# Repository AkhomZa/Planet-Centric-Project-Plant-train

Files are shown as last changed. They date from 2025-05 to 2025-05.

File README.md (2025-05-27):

# Planet Centric Project : Plant train
โปรเจคนี้เป็นของวิชา FRA503 : PLANET-CENTRIC ROBOTICS &amp; INNOVATION

ผูัจัดทำ : อาคม สนธิขันธ์

# แนวคิดและที่มา
การปลูกต้นไม้บนโต๊ะทำงานไม่เพียงช่วยสร้างบรรยากาศที่ร่มรื่นและน่าอยู่เท่านั้น แต่ยังมีส่วนช่วยฟอกอากาศและส่งเสริมสุขภาพจิตของผู้ปฏิบัติงานอีกด้วย หลายงานวิจัยชี้ว่าการมีต้นไม้ในพื้นที่ทำงานสามารถลดความเครียด เพิ่มสมาธิ และสร้างความรู้สึกผ่อนคลาย ส่งผลให้เกิดประสิทธิภาพในการทำงานที่ดีขึ้น ดังนั้นแนวคิดการปลูกต้นไม้บนโต๊ะทำงานจึงเป็นจุดเริ่มต้นของโครงการนี้

ในปัจจุบันมีนวัตกรรมต้นไม้แบบอัจฉริยะ เช่น Smart Plant Ivy ซึ่งรวมเซนเซอร์วัดค่าความชื้น แสง และระบบควบคุมต่างๆ ไว้ในกระถางต้นไม้เดียว อย่างไรก็ตาม หากต้องการปลูกหลายต้น ก็จำเป็นต้องมีเซนเซอร์และอุปกรณ์แยกในแต่ละกระถาง ซึ่งทำให้ต้นทุนสูงขึ้นอย่างไม่จำเป็น

เพื่อแก้ปัญหาดังกล่าว ผู้จัดทำจึงเสนอแนวคิดการรวมระบบเซนเซอร์ไว้ในจุดเดียว และออกแบบให้แต่ละกระถางสามารถใช้เซนเซอร์ร่วมกันได้ เพื่อลดค่าใช้จ่ายและความซับซ้อนของระบบ

อีกหนึ่งปัญหาที่พบในการปลูกต้นไม้บนโต๊ะทำงานคือ “ตำแหน่งการวางกระถาง” หากวางไว้ในบริเวณที่แสงไม่เพียงพอ ต้นไม้อาจไม่เจริญเติบโตหรือตายได้

จากปัญหาและแนวคิดข้างต้น จึงได้ออกแบบนวัตกรรม "กระถางต้นไม้เคลื่อนที่ได้" ซึ่งสามารถเคลื่อนย้ายตัวเองเพื่อหาตำแหน่งที่มีแสงเหมาะสม และสามารถวัดค่าต่างๆ ผ่านเซนเซอร์ส่วนกลางร่วมกันได้ ช่วยเพิ่มโอกาสในการเจริญเติบโตของพืช และยังลดต้นทุนในการติดตั้งระบบเซนเซอร์อีกด้วย

## Plant train

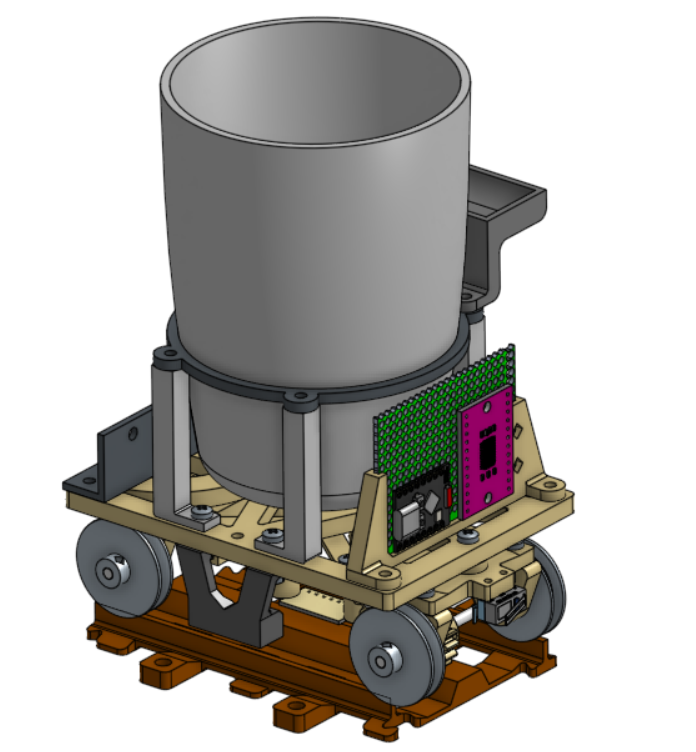
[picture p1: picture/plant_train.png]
Plant train


## Water station

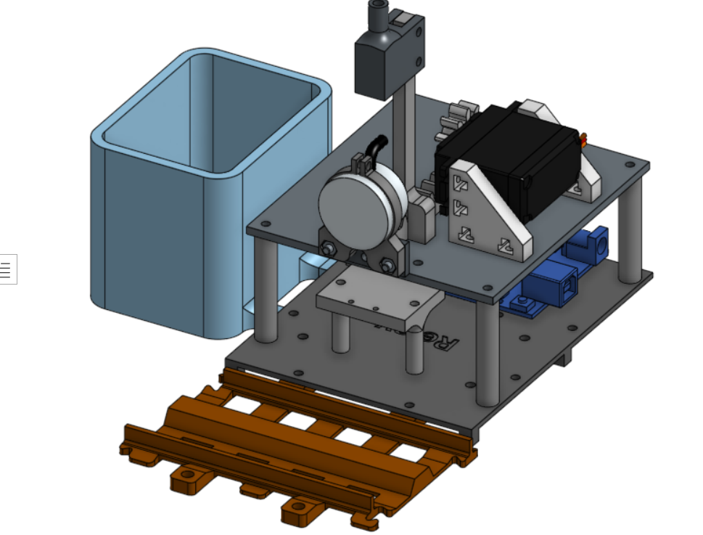
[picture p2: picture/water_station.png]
Water station


## Overview wiring diagram
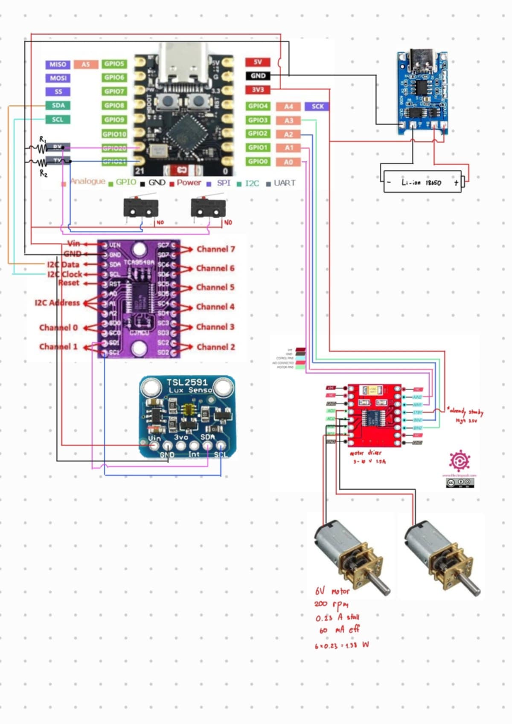
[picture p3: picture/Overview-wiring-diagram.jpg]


## Electronics Component

**"On Plant train"**

- **Microcontroller:** ESP32 C3 mini

- **Motor Driver:** DRV8833

- **Lux sensor:** BH1750 (วัดความเข้มของแสง)

- **Color sensor:** TCS34725 (สำหรับอ่านแถบสีคำสั่ง)

- **I2C Multiplexer:** TCA9548A (สำหรับขยายช่องสัญญาณ I2C)

- **Lithium Charging module:** USB TYPE-C charger TP4056 1A (สำหรับชาร์จแบตเตอรี่ลิเธียม 18650)

- **ฺBattery:** 186500 Lithium Battery

**"On Water station"**

- **Microcontroller:** Arduino Uno

- **Water level non contack sensor:** XKCY25 (วัดระดับน้ำแบบไร้สัมผัส)

- **Hall effect magnetic sensor:** KY-035 (สำหรับตรวจเช็คการมาของรถไฟ)

- **Relay module:** 4 channel-Relay

- **DC Water pump**

- **Servo motor:** MG995 180 degree servo motor

## Mechanics Part

- **3D Print part**

- **Shaft diameter:** 3 mm

- **Bearing:** 603ZZ

- **O-ring:** ID 19 mm 2 mm thickness

- **Heat brass insert**

- **Bolt&Nuts :** ส่วนใหญ่เป็นขนาด M3 ยาว 6-12 mm ขึ้นอยู่กับส่วนไหนใส่ได้ยาวแค่ไหน

## อุปกรณ์ที่เหลือ

- กระถางรดน้ำเอง แบบใช้หลักการกาลักน้ำ
- สายยางซิลิโคน ID 7 mm

## ภาพ CAD การประกอบคร่าวๆ และส่วนประกอบ

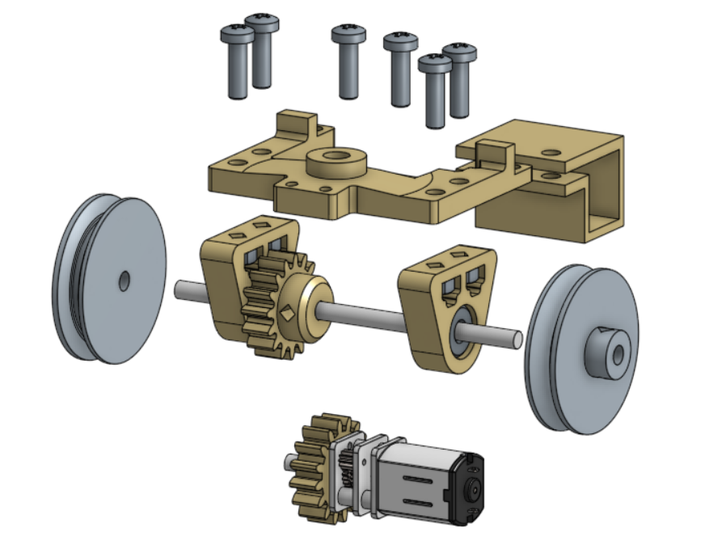
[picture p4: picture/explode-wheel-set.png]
Explode view of wheel set


- ใช้ shaft ประมาณ 65mm
- ใช้ set screw M3 กับล้อและเฟือง
- ประกอบส่วนล้อก่อนแล้วประกอบชุดมอเตอร์ทีหลัง
- ใส่เฟืองกับมอเตอร์ก่อนประกอบเข้าด้วยกัน
- ใช้ Screw M3*10 และ nut เป็นส่วนใหญ่

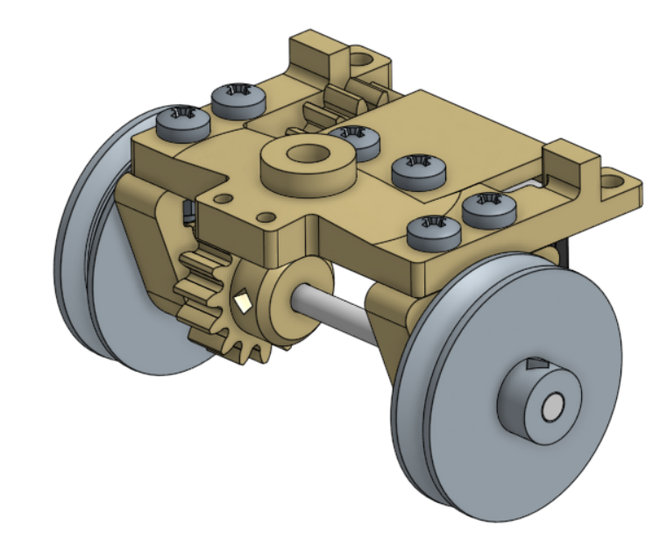
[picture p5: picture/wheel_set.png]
Wheel set assembly


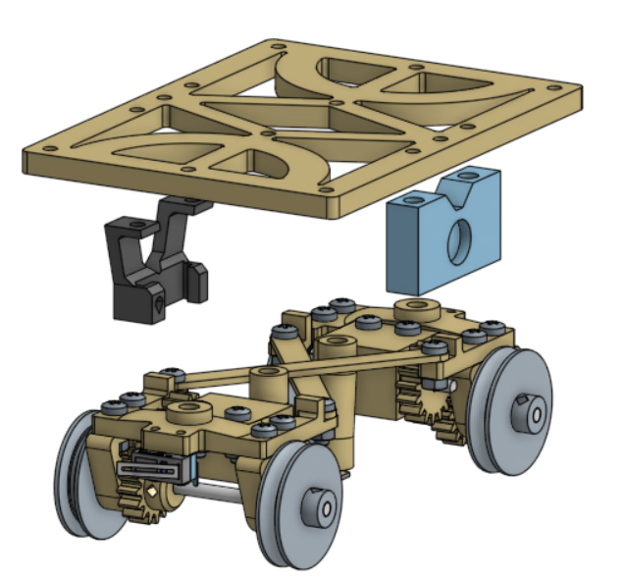
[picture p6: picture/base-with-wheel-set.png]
Base with wheel set assembly


- ประกอบ wheel set กับ base ด้วยสกรู M3*10 mm มันจะยึดไม่แน่นเพื่อให้รถสามารถเลี้ยวได้ สามารถเพิ่มเติมด้วยการใส่ น้ำยาล็อกเกลียวเพิ่ม เพื่อให้สกรูไม่คลาย หรือออกแบบใหม่ให้ดีขึ้น

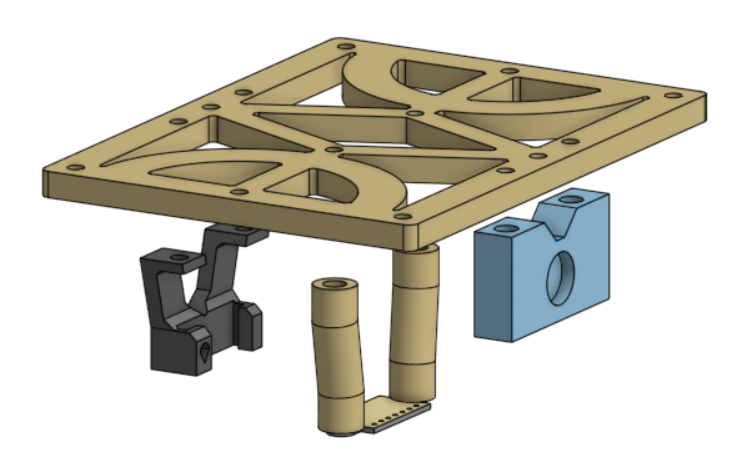
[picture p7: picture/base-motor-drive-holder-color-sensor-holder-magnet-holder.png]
Base with motor driver/magnet/color sensor holder


- spacer ยึด color sensor ทั้งสองด้านมี heat brass insert อยู่
- ประกับเซนเซอร์ก่อนค่อยประกอบกับ base
- ตัวยึด motor drive แนะนำให้ใส่ก่อนโดยการเลื่อนเข้าไปแล้วขันล็อกด้วย set screw M3 ก่อนแล้วบัดกรีสายไฟเข้าไป
- ตัวยึดแม่เหล็ก ก่อนใส่เช็คด้านของแม่เหล็กก่อน เพราะเอาออกยาก

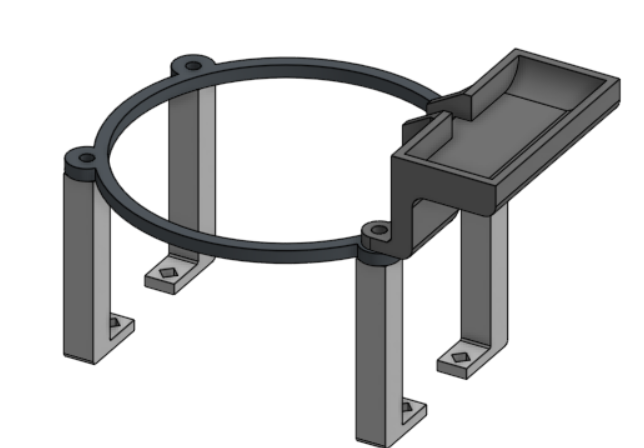
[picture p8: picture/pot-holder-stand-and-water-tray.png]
Pot holder with watering tray on top base


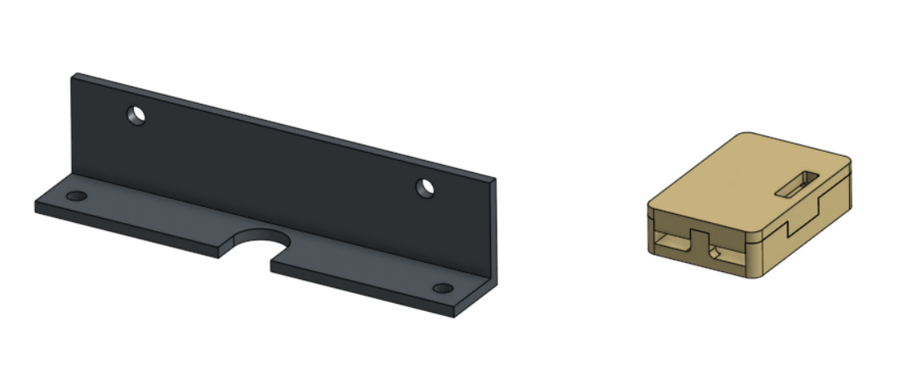
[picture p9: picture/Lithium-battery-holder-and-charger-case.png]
battery holder on the back and charger case


- ใช้กับรังถ่านแบตเตอรี่ลิเธียม 18650 แบบไม่มีสปริงขดลวด
- ใช้ Screw Tapor M3 แล้วล็อกด้วย nut
- บัดกรีสายไฟกับชุดชาร์จก่อนประกอบกับ case แล้วติดด้วยกาวสองหน้า

**ข้อสังเกตและการแนะนำ**
- รูขนาดประมาณ 4.5 mm สำหรับใส่ heat brass insert
- เริ่มประกอบจาก wheel set ก่อน ประกอบที่ล็อกมอเตอร์ และปิดป้ายด้วย X beam เชื่อม Wheel set 2 ชุดเข้าด้วยกัน

Water station

- ประกอบกับรางตรงเฉพาะแบบในรูปเท่านั้น
- ติดตั้ง relay และ arduino uno ก่อน ตามด้วยประกอบชั้นสองตาม
- ประกอบ servo โดยเซ็ตตำแหน่ง 0 องศาก่อน แล้วเลื่อน rack gear เข้าไป จุดท้ายประกอบ pinion gear ตามเข้าไป
  *จำเป็นออกแบบตัวติดตั้ง Hall effect magnetic sensor ใหม่

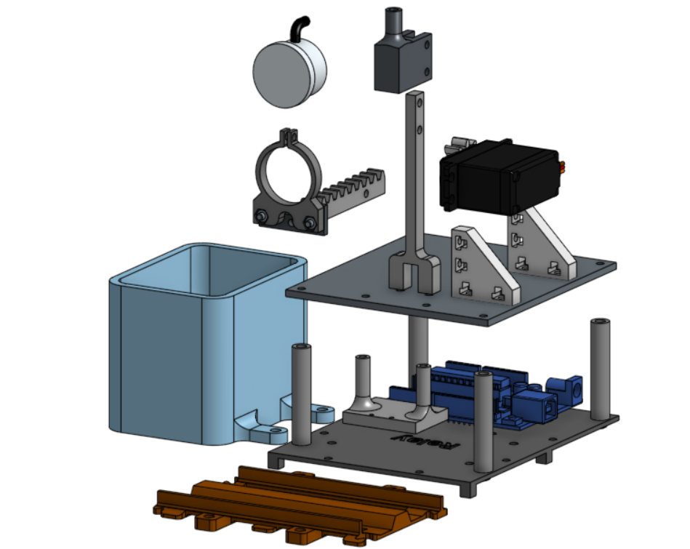
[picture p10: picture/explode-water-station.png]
Explode view Water station


## Code สำหรับตัวรถ

ก่อน upload เช็คหัวข้อ USB CDC On Boot หากใช้โปรแกรม Arduino IDE

```bash
#include <Wire.h>
#include <Adafruit_Sensor.h>
#include <Adafruit_TSL2591.h>
#include "TCA9548A.h"  //I2C multiplexer module
#include "Adafruit_TCS34725.h"
#include <BH1750.h>  //lux sensor module

#define commonAnode true
#define pwmA 0
#define in1A 1
#define in2A 2
#define pwmB 3
#define in1B 5
#define in2B 4
#define frontLimit 20
#define backLimit 21

TCA9548A mux;  //call multiplexer as mux

int LuxsensorState = 0;
unsigned long LuxlastReadTime = 0;
const unsigned long LuxsensorDelay = 5;

int ColorsensorState = 0;
unsigned long ColorlastReadTime = 0;
const unsigned long ColorsensorDelay = 5;

int countSun, countWater = 0;
bool trickDone = false;
float red, green, blue;
int WhiteTableOnRail_config[3] = {83,98,68};
int WhiteCode[3] = {70,101,75};
int RedCode[3] = {120,75,62};
int timeout = 30000;
float LeftFront, LeftBack, RightFront, RightBack; //for luxData

// Look from top view
//       front(B)
//      0 ------ 3
//          ||
//   left   ||   right
//          ||
//      1 ------ 2
//        back(A)
BH1750 lightMeter0(0x23);
BH1750 lightMeter1(0x23);
BH1750 lightMeter2(0x23);
BH1750 lightMeter3(0x23);

//color sensor config
Adafruit_TCS34725 tcs = Adafruit_TCS34725(TCS34725_INTEGRATIONTIME_50MS, TCS34725_GAIN_4X);

Adafruit_TSL2591 tsl = Adafruit_TSL2591(2591);

void lux_read(float* LeftFront, float* LeftBack, float* RightFront, float* RightBack);      // ประกาศฟังก์ชันที่อยู่ในไฟล์อื่น
void engine_start();  // ถ้าเรียกใช้ก็ประกาศไว้ด้วย

/* TCA9548A multi sent 0x29 for communicate TSL2591 so need to command to tca to tell tsl*/
void setup() {
  delay(1000);
  Serial.begin(115200);
  pinMode(pwmA, OUTPUT);
  pinMode(pwmB, OUTPUT);
  pinMode(in1A, OUTPUT);
  pinMode(in2A, OUTPUT);
  pinMode(in1B, OUTPUT);
  pinMode(in2B, OUTPUT);
  pinMode(frontLimit, INPUT);
  pinMode(backLimit, INPUT);
  Wire.begin(8, 9);  // GPIO 8 = SDA, GPIO 9 = SCL
  mux.begin(Wire);   // Use Wire instance
  mux.closeAll();    // Optional: reset all channels

  Serial.println(F("Starting"));

  //check lux sensor's read

  mux.openChannel(0);
  if (lightMeter0.begin(BH1750::CONTINUOUS_HIGH_RES_MODE)) {
    Serial.println(F("Left_Front sensor checked!"));
  } else {
    Serial.println(F("Left_Front sensor error!"));
  }
  delay(150);

  mux.openChannel(1);
  if (lightMeter1.begin(BH1750::CONTINUOUS_HIGH_RES_MODE)) {
    Serial.println(F("Left_Back sensor checked!"));
  } else {
    Serial.println(F("Left_Back sensor error!"));
  }
  delay(150);

  mux.openChannel(2);
  if (lightMeter2.begin(BH1750::CONTINUOUS_HIGH_RES_MODE)) {
    Serial.println(F("Right_Back sensor checked!"));
  } else {
    Serial.println(F("Right_Back sensor error!"));
  }
  delay(150);

  mux.openChannel(3);
  if (lightMeter3.begin(BH1750::CONTINUOUS_HIGH_RES_MODE)) {
    Serial.println(F("Right_Front sensor checked!"));
  } else {
    Serial.println(F("Right_Front sensor error!"));
  }
  delay(150);

  //check color sensor's status
  mux.openChannel(7);
  if (tcs.begin()) {
    Serial.println(F("TCS34725 COLOUR checked!"));
  } else {
    Serial.println(F("TCS34725 COLOUR not found!"));
  }
  delay(150);
  goWaterStation();
}

void loop() {
  int start_time = millis();
  while(millis() - start_time < 10000){
    followLight();
  }
  goWaterStation();
  delay(2000);

  // color_read();
}

/*funtion check water*/
void water_level() {
  /*506 mai jer
4095 jer*/
  if (analogRead(A0) >= 2300) {
    Serial.println("Water detected");
  } else {
    Serial.println("No Water");
  }
  delay(1000);
  // Serial.println(analogRead(A0));
}

/*function colour code*/
void track() {
  while (1) {
    if (digitalRead(frontLimit) == 1 && digitalRead(backLimit) == 1) {
      goFront(255, 255);
    } else if (digitalRead(frontLimit) == 0 && digitalRead(backLimit) == 1) {
      goBack(255, 255);
    } else if (digitalRead(frontLimit) == 0 && digitalRead(backLimit) == 0) {
      break;
    }
  }
}

void checkLimit() {  //limit switch active low
  if (digitalRead(frontLimit) == 0 && digitalRead(backLimit) == 1) {
    Serial.println("Front Limit Trigger");
  } else if (digitalRead(frontLimit) == 1 && digitalRead(backLimit) == 0) {
    Serial.println("Back Limit Trigger");
  } else if (digitalRead(frontLimit) == 0 && digitalRead(backLimit) == 0) {
    Serial.println("Both Limit Trigger");
  }
}

/* new code after test on I2C*/
void configureSensor(void) {
  tsl.setGain(TSL2591_GAIN_MED);
  tsl.setTiming(TSL2591_INTEGRATIONTIME_300MS);

  Serial.println(F("Sensor configured."));
}

void goFront(int MotorSpeed1, int MotorSpeed2) {
  int MotorStartSpeed1 = round((MotorSpeed1) / 3);
  int MotorStartSpeed2 = round((MotorSpeed2) / 3);
  digitalWrite(in1A, LOW);
  digitalWrite(in2A, HIGH);
  analogWrite(pwmA, MotorStartSpeed1);
  delay(50);
  digitalWrite(in1B, LOW);
  digitalWrite(in2B, HIGH);
  analogWrite(pwmB, MotorStartSpeed2);
  delay(100);
  analogWrite(pwmA, MotorSpeed1);
  delay(10);
  analogWrite(pwmB, MotorSpeed2);
}

void goBack(int MotorSpeed1, int MotorSpeed2) {
  int MotorStartSpeed1 = round((MotorSpeed1) / 3);
  int MotorStartSpeed2 = round((MotorSpeed2) / 3);
  digitalWrite(in1A, HIGH);
  digitalWrite(in2A, LOW);
  analogWrite(pwmA, MotorStartSpeed1);
  delay(50);
  digitalWrite(in1B, HIGH);
  digitalWrite(in2B, LOW);
  analogWrite(pwmB, MotorStartSpeed2);
  delay(100);
  analogWrite(pwmA, MotorSpeed1);
  delay(10);
  analogWrite(pwmB, MotorSpeed2);
}

void stop() {  // a is time in millisecond
  digitalWrite(in1A, LOW);
  digitalWrite(in2A, LOW);
  digitalWrite(in1B, LOW);
  digitalWrite(in2B, LOW);
}

void engine_start() {

  bool flag = false;
  Serial.println(digitalRead(frontLimit));
  Serial.println(digitalRead(backLimit));

  while (1) {
    if (digitalRead(frontLimit) == 0 && digitalRead(backLimit) == 0) {  //active low
      Serial.println("Ready");
      flag = true;
      break;
    } else
      Serial.println("Please hold 2 button to start!");
    delay(100);
  }
}

void color_read() {
  static int color_read[3];
  static int color_treshold = 5;

  mux.writeRegister(TCA_CHANNEL_7);
  delay(10);
  tcs.getRGB(&red, &green, &blue);
  color_read[0] = red;
  color_read[1] = green;
  color_read[2] = blue;
  delay(5);
  Serial.print("R:\t");
  Serial.print(int(red));
  Serial.print("\tG:\t");
  Serial.print(int(green));
  Serial.print("\tB:\t");
  Serial.print(int(blue));
  Serial.print("\n");
  if (abs(color_read[0] - WhiteCode[0]) < color_treshold && abs(color_read[1] - WhiteCode[1]) < color_treshold && abs(color_read[2] - WhiteCode[2]) < color_treshold) {
    Serial.print("White");
  }
  if (abs(color_read[0] - RedCode[0]) < color_treshold && abs(color_read[1] - RedCode[1]) < color_treshold && abs(color_read[2] - RedCode[2]) < color_treshold) {
    Serial.print("Red");
  }
  else {
    Serial.print("none");
  }
}

void goWaterStation() {
  int color_treshold = 5;
  unsigned long start_time = 0;  //time
  goFront(160,160);
  while (1) {
    color_read();
    int color_read[3] = { int(red), int(green), int(blue) };
    if (abs(color_read[0] - WhiteCode[0]) < color_treshold && abs(color_read[1] - WhiteCode[1]) < color_treshold && abs(color_read[2] - WhiteCode[2]) < color_treshold) {
      Serial.print("It's White");
      Serial.print("\n");
      goFront(60,60);
    }
    else if (abs(color_read[0] - RedCode[0]) < color_treshold && abs(color_read[1] - RedCode[1]) < color_treshold && abs(color_read[2] - RedCode[2]) < color_treshold) {
      Serial.print("It's Red");
      Serial.print("\n");
      stop();
      delay(15000);
      break;
    }
    if (millis() - start_time > timeout) {
      Serial.println("Time out! Cancel action");
      stop();
      break;
    }
  }
  goFront(100,100);
  delay(2000);
  stop();
}

void lux_read(float* LeftFront, float* LeftBack, float* RightFront, float* RightBack) {
  float lux0, lux1, lux2, lux3, cf_med;

  cf_med = 0.00062594;

  // Read from sensor 0 (channel 0)
  mux.openChannel(0);
  delay(10);  // Wait for measurement time
  if (lightMeter0.measurementReady()) {
    *LeftFront = lightMeter0.readLightLevel() * cf_med;
  }
  mux.closeAll();

  // Read from sensor 1 (channel 1)
  mux.openChannel(1);
  delay(10);  // Wait for measurement time
  if (lightMeter1.measurementReady()) {
    *LeftBack = lightMeter1.readLightLevel() * cf_med;
  }
  mux.closeAll();

  // Read from sensor 2 (channel 2)
  mux.openChannel(2);
  delay(10);  // Wait for measurement time
  if (lightMeter2.measurementReady()) {
    *RightBack = lightMeter2.readLightLevel() * cf_med;
  }
  mux.closeAll();

  // Read from sensor 3 (channel 3)
  mux.openChannel(3);
  delay(10);  // Wait for measurement time
  if (lightMeter3.measurementReady()) {
    *RightFront = lightMeter3.readLightLevel() * cf_med;
  }
  mux.closeAll();

  /*/         front
          0 ------ 3
              ||
       left   ||   right
              ||
          1 ------ 2
             back       /*/

  delay(10);  // Wait before next loop
}

void followLight() {
  // unsigned long start_time = 0;  //time
  // bool flag = true;
  // int threshold = 5;
  // int max_sum = 0;
  // int sum = 0;
  // int cf_med = 0.00062594;
  // while (flag) {
  //   lux_read(&LeftFront, &LeftBack, &RightFront, &RightBack);
  //   LeftFront = (LeftFront*1600);
  //   RightFront = (RightFront*1600);
  //   LeftBack = (LeftBack*1600);
  //   RightBack = (RightBack*1600);
  //   Serial.println(LeftFront);
  //   Serial.println(RightFront);
  //   Serial.println(LeftBack);
  //   Serial.println(RightBack);
  //   Serial.println("\n");
  //   int sum = LeftBack + RightBack + LeftFront + RightFront;
  //   // int max_lightSource_dir = max(max(LeftFront,LeftBack),max(RightFront,RightBack)));

  //   if ((LeftFront + RightFront) - (LeftBack + RightBack) > threshold ) {
  //     goFront(255, 255);
  //     if ((LeftFront + RightFront) - (LeftBack + RightBack) < threshold ){
  //       goFront(50,50);
  //     }
  //     else {
  //       stop();
  //     }
  //   }
  //   else if ((LeftBack + RightBack) - (LeftFront + RightFront) > threshold ){
  //     goBack(255,255);
  //     if ((LeftFront + RightFront) - (LeftBack + RightBack) < threshold ){
  //       goBack(50,50);
  //     }
  //     else {
  //       stop();
  //     }
  //   }
  //   if (sum > max_sum){
  //     int max_sum = sum;
  //   }
  //   // if (millis() - start_time > timeout) {
  //   //   Serial.println("Time out! Cancel action");
  //   //   stop();
  //   //   break;
  //   // }

  // }
  static float LeftFront, LeftBack, RightFront, RightBack;
  static unsigned long max_sum = 0;
  static unsigned long start_time = millis();
  static unsigned long timeout = 10000;

  switch (LuxsensorState) {
    case 0:  // READ_LF
      mux.openChannel(0);
      LuxlastReadTime = millis();
      LuxsensorState = 1;
      break;

    case 1:  // WAIT_LF
      if (millis() - LuxlastReadTime >= LuxsensorDelay) {
        if (lightMeter0.measurementReady()) {
          LeftFront = lightMeter0.readLightLevel() * 0.00062594 * 1600;
        }
        mux.closeAll();
        LuxsensorState = 2;
      }
      break;

    case 2:  // READ_LB
      mux.openChannel(1);
      LuxlastReadTime = millis();
      LuxsensorState = 3;
      break;

    case 3:  // WAIT_LB
      if (millis() - LuxlastReadTime >= LuxsensorDelay) {
        if (lightMeter1.measurementReady()) {
          LeftBack = lightMeter1.readLightLevel() * 0.00062594 * 1600;
        }
        mux.closeAll();
        LuxsensorState = 4;
      }
      break;

    case 4:  // READ_RB
      mux.openChannel(2);
      LuxlastReadTime = millis();
      LuxsensorState = 5;
      break;

    case 5:  // WAIT_RB
      if (millis() - LuxlastReadTime >= LuxsensorDelay) {
        if (lightMeter2.measurementReady()) {
          RightBack = lightMeter2.readLightLevel() * 0.00062594 * 1600;
        }
        mux.closeAll();
        LuxsensorState = 6;
      }
      break;

    case 6:  // READ_RF
      mux.openChannel(3);
      LuxlastReadTime = millis();
      LuxsensorState = 7;
      break;

    case 7:  // WAIT_RF
      if (millis() - LuxlastReadTime >= LuxsensorDelay) {
        if (lightMeter3.measurementReady()) {
          RightFront = lightMeter3.readLightLevel() * 0.00062594 * 1600;
        }
        mux.closeAll();
        LuxsensorState = 8;
      }
      break;

    case 8:
      {  // PROCESS
        int sum = LeftFront + LeftBack + RightFront + RightBack;
        Serial.println(LeftFront);
        Serial.println(RightFront);
        Serial.println(LeftBack);
        Serial.println(RightBack);
        Serial.println();

        int threshold = 80;

        if (sum > max_sum) {
          max_sum = sum;
        }

        // การเคลื่อนที่พื้นฐาน
        if ((LeftFront + RightFront) - (LeftBack + RightBack) > threshold) {
          goFront(255, 255);
        } else if ((LeftBack + RightBack) - (LeftFront + RightFront) > threshold) {
          goBack(255, 255);
        }
        // else if (abs((LeftBack + RightBack) - (LeftFront + RightFront)) < 10){
        //   stop(); // ตำแหน่งสมดุลแสง
        // }
        else {
          Serial.println("Unclear direction. Stopping.");
          stop();
          max_sum = 0;
        }

        if (millis() - start_time > timeout) {
          Serial.println("Timeout");
          stop();
          LuxsensorState = 0;  // reset
          break;
        }

        // ถ้าความสว่างเริ่มลดลง แสดงว่าเลยแสงหรืออยู่ใกล้แสงมากพอ => หยุด
        if (max_sum - sum < threshold) {
          Serial.println("Reached light source. Stopping.");
          stop();
          max_sum = 0;
          LuxsensorState = 0;
          return;
        }

        LuxsensorState = 0;  // เริ่มรอบใหม่
        break;
      }
  }
}

```

## Code สำหรับตัวสถานี

```bash
int halSensor = A5;  //halSensor pin
int waterSensor = A0;
int relay = 7;
int val;         //numeric variable
int kep_water = 1;
bool detecting = false;
#include <Servo.h>
Servo myservo;  //ตัวแปรแทน Servo
void setup() {

	Serial.begin(115200);
	pinMode(halSensor, INPUT);  //hal halSensor
	pinMode(waterSensor, INPUT);
	pinMode(relay, OUTPUT);

	myservo.attach(9);
	myservo.write(0);  // หมุนออก
	delay(1000);

	digitalWrite(relay,HIGH);

	// myservo.detach();
	// delay(1000);
	// Serial.println(myservo.read());
	// myservo.attach(9);
	// Serial.println(myservo.read());
	// myservo.write(50);  // หมุนเก็บ
	// delay(2500);
	// Serial.println(myservo.read());
	// myservo.detach();
	
}

void loop() { // 0-70
	Serial.println(digitalRead(waterSensor));
	int state = 0;

	if (abs(analogRead(halSensor)-810) < 30){
		// myservo.write(70);  // หมุนออก
		Serial.println("yes");
		delay(3000);
		if (abs(analogRead(halSensor)-810) < 30){
			myservo.write(80);
			delay(1000);
			int state = digitalRead(waterSensor);
			delay(1000);
			myservo.write(0);
			delay(1000);
			if (state == 0){
				delay(9000);
			}
			else if(state == 1) {
				digitalWrite(relay,LOW);
				delay(5000);
				digitalWrite(relay,HIGH);
				delay(4000);
			}
		}
	}
	else if (analogRead(halSensor) < 700){
		myservo.write(0);
	}
	delay(500);
}
```

**ฟังก์ชั่นการทำงาน ตอนนี้**
- ตรวจหาทิศทางของแสงแล้ววิ่งไป
- เข้าสถานีเพื่อเติมน้ำ
- มี micro swtitch กันชนจากรถคันอื่นได้

**สิ่งที่วางแผนไว้**
- วัดค่าแสงแล้วเก็บเป็น PPFD สะสมทั้งวัน
- สถานีรับแสงเพิ่มเติม หากไม่รับแสงไม่พอในระหว่างวัน
- ใช้งานได้มากกว่า 1 คัน
  
**ปัญหาที่พบเจอ และแนวทางแก้ไข และข้อเสนอแนะ**
- เนื่องจากผู้จัดทำใช้สายไฟขนาด 30 AWG ซึ่งบางจุดมีกระแสเยอะ ทำให้แรงดันตก พิจารณาเปลี่ยนสายไฟที่เลี้ยงวงจรทั้งหมดและเลี้ยงมอเตอร์ให้มีจนาดใหญ่ขึ้น
- มอเตอร์ยังไม่ได้บัดกรีสายไฟ เป็นเพียงการพันรอบขั้วมอเตอร์แล้วติดกาวทับเท่านั้น แนะนำว่าบัดกรีก่อนแล้วติดกาวซ้ำเพื่อกันสายขาดบริเวณขั้ว
- เนื่องจากงานนี้เป็น Prototype แผงวงจรจึงเป็นบอร์ดไข่ปลา สามารถออกแบบเป็น PCB สำเร็จรูปเพื่อความคงทน เสถียรและประหยัดพื้นที่
- เพิ่มขนาดแหล่งพลังงาน หรือเปลี่ยน microcontroller เพื่อทำให้กินพลังงานน้อยลง หรือออกแบบรางที่สามารถจ่ายไฟได้
- สถานีน้ำ การตรวจสอบรถที่เข้ามาด้วย Hall effect magnetic sensor ยังไม่สเถียร เนื่องจากการออกแบบที่ยึดไม่ดี
- ไม่มี swtich เปิด-ปิดไฟเลี้ยงอุปกรณ์ ทำให้ไม่สามารถชาร์จแบตเตอรี่ได้

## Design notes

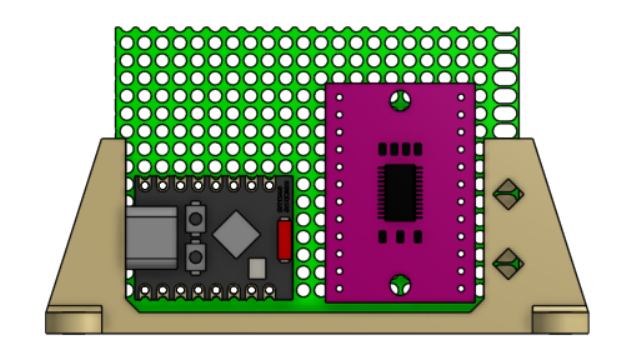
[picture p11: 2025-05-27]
picture/Electronic-board-holder.png

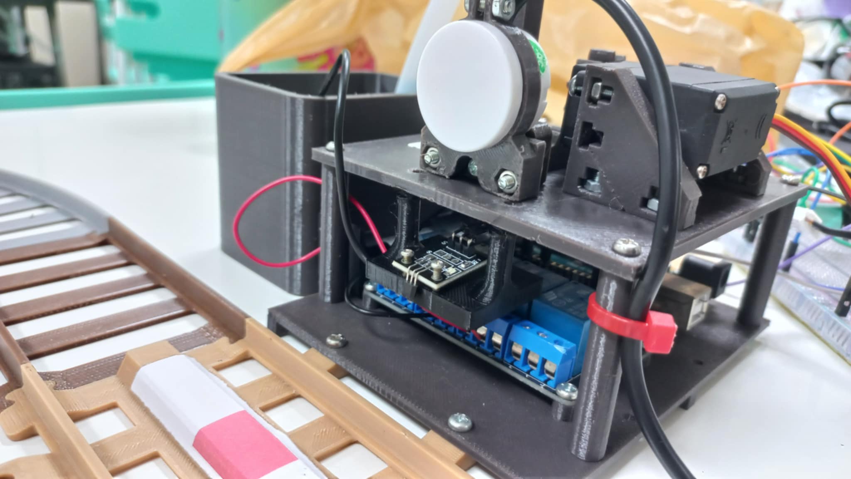
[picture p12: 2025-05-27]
picture/real_water_station.jpg

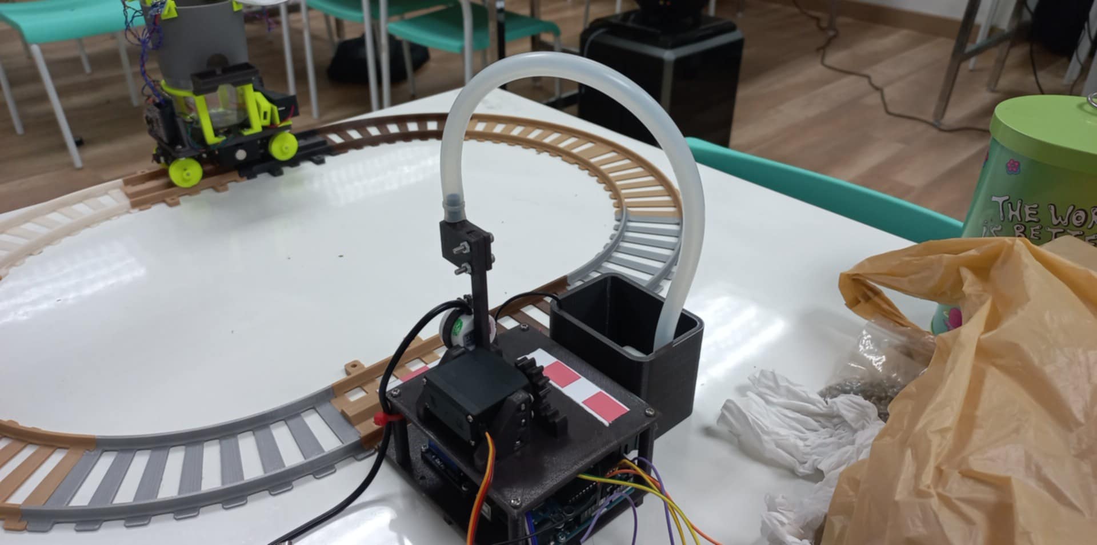
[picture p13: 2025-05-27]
picture/watering_system_water_station.jpg

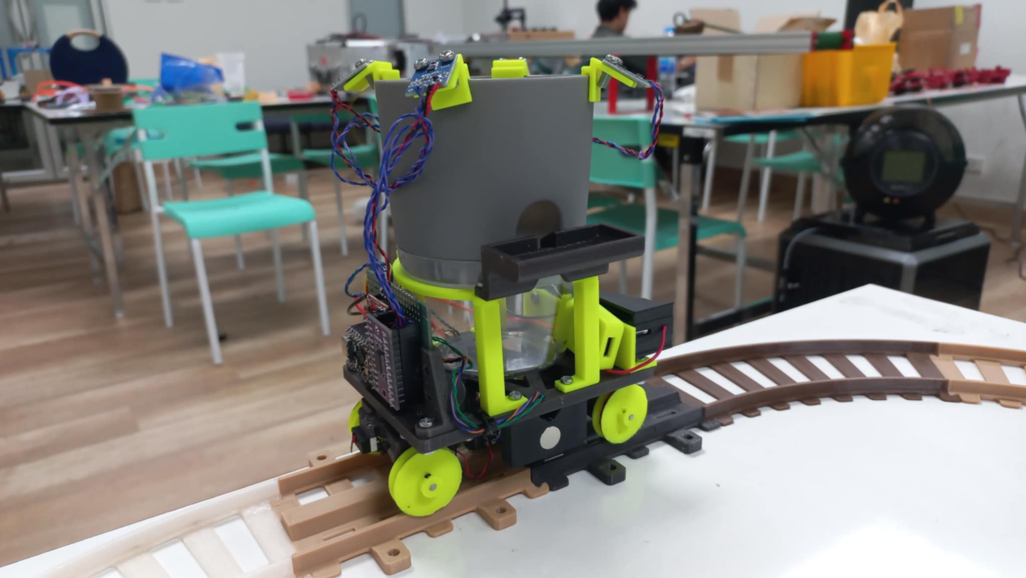
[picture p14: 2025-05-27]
picture/magnet_on_side_view_plant_train.jpg

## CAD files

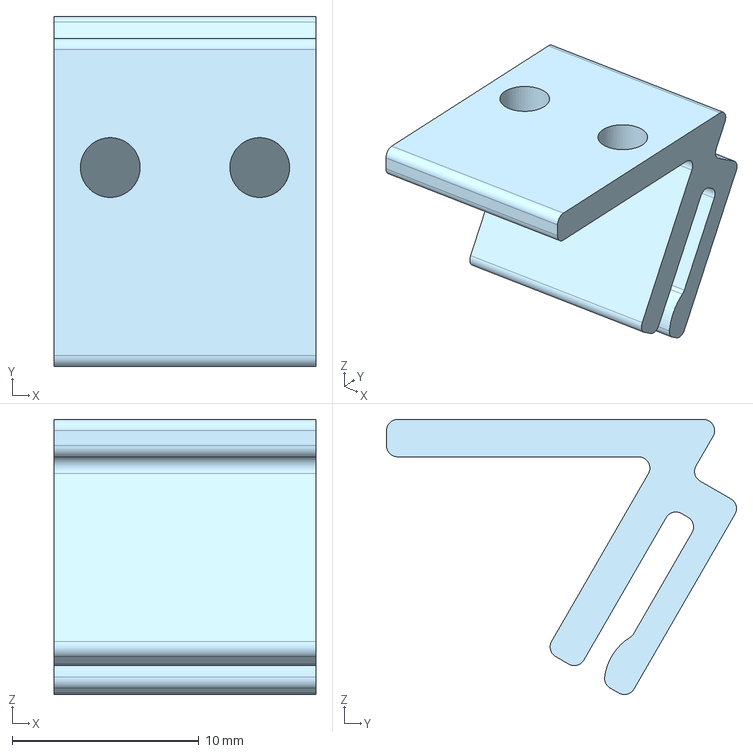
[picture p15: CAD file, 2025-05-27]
CAD&model/lux_sensor_clip_pot.step
14.0 x 18.7 x 14.7 mm

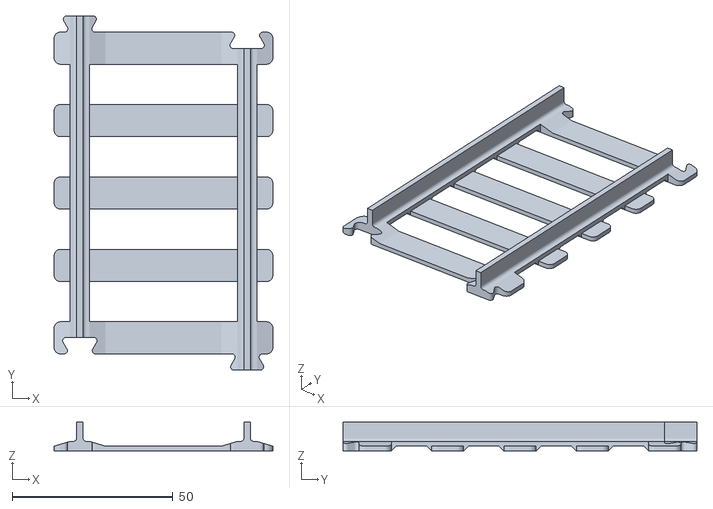
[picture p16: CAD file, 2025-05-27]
CAD&model/rail/100straight (1).stl
68.0 x 110.0 x 9.00

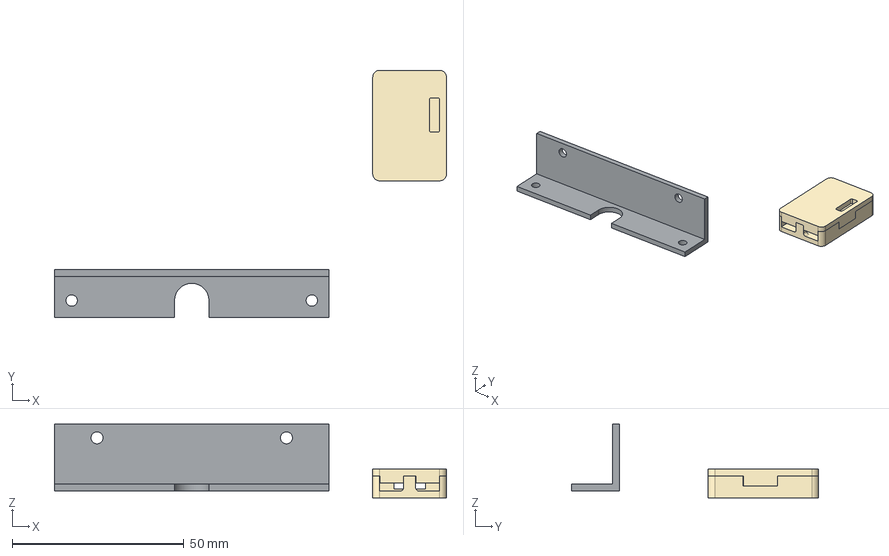
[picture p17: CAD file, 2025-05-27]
CAD&model/Lithium_holder&case.step
114.2 x 72.1 x 21.5 mm

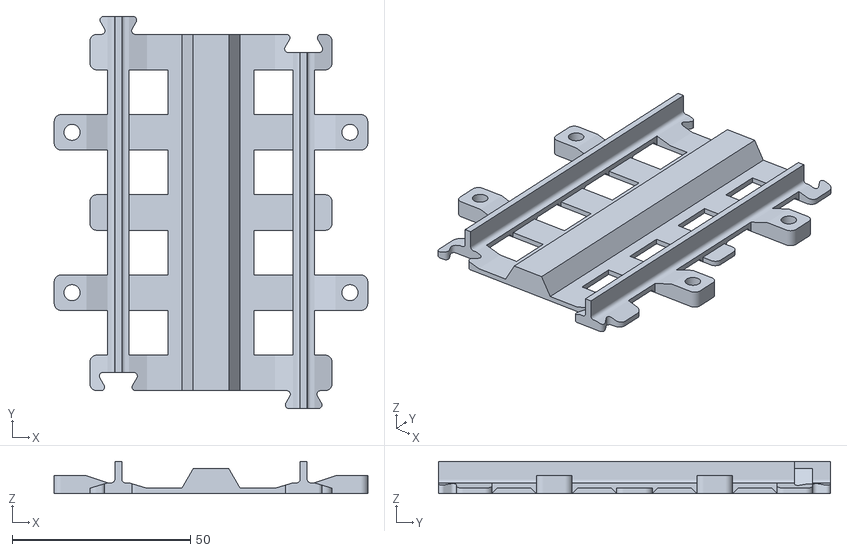
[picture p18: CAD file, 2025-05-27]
CAD&model/rail/100straight_color_code (1).stl
88.0 x 110.0 x 9.00

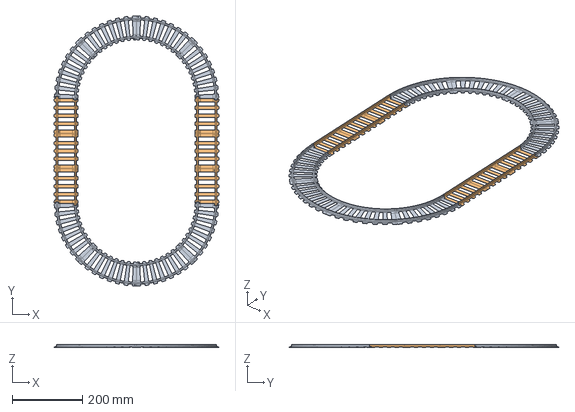
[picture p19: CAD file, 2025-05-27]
CAD&model/rail/rail_assem.step
468.0 x 768.0 x 9.00 mm
R200-45deg x 8
100straight x 6

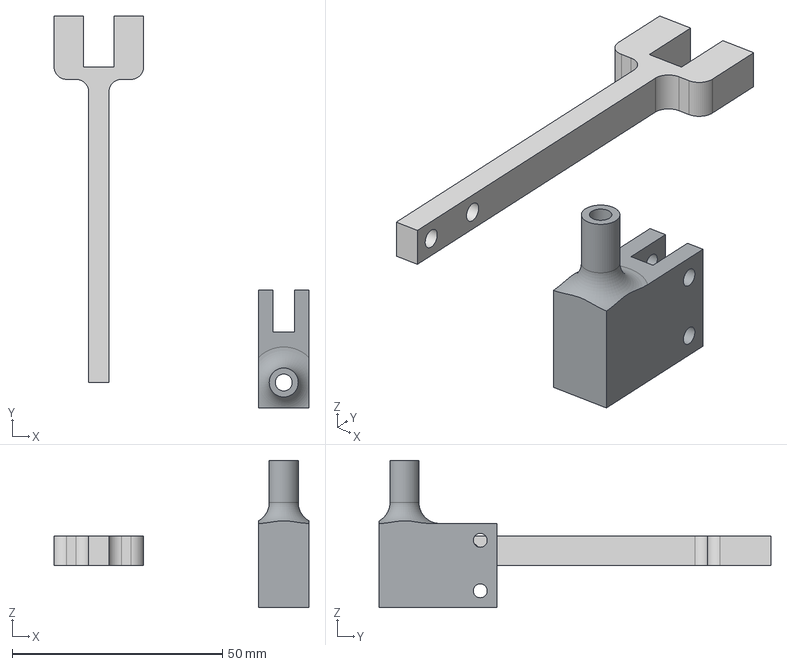
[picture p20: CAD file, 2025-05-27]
CAD&model/watering_part.step
60.6 x 93.0 x 35.0 mm

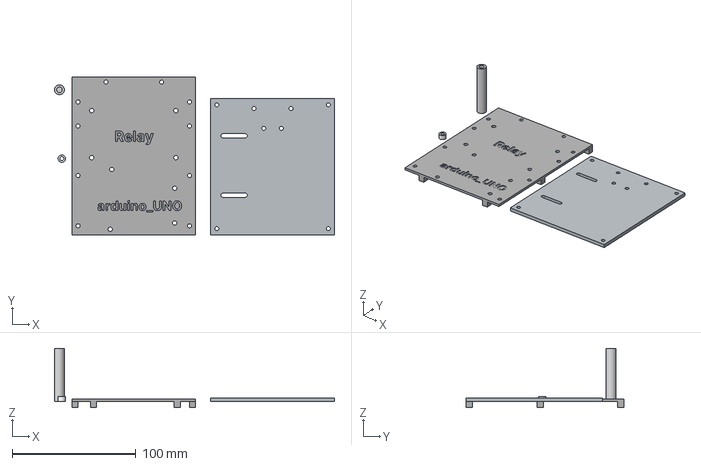
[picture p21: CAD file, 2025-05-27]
CAD&model/station_part.step
226.0 x 127.3 x 48.0 mm

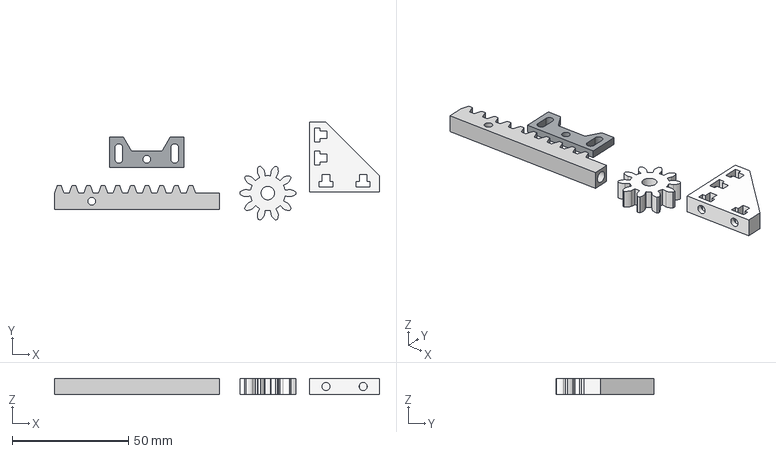
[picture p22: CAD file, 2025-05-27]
CAD&model/servo_part_set.step
139.5 x 42.1 x 7.00 mm

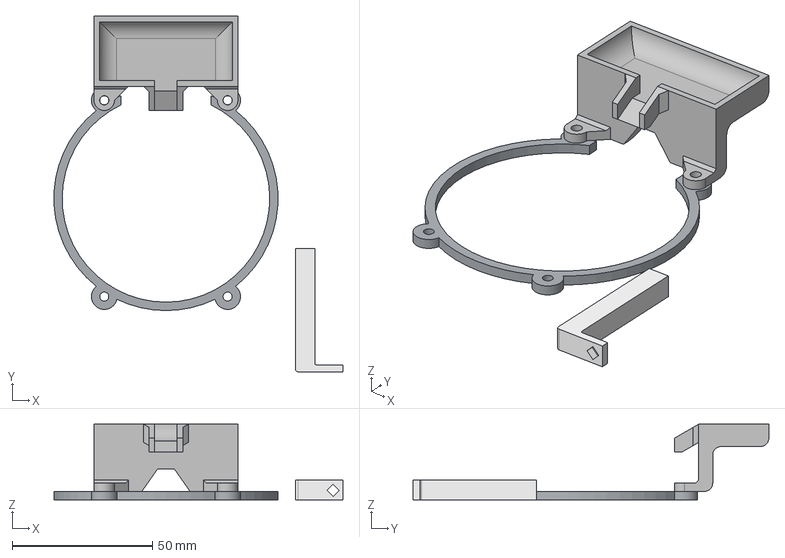
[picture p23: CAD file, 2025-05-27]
CAD&model/pot_holder.step
103.1 x 126.9 x 27.0 mm

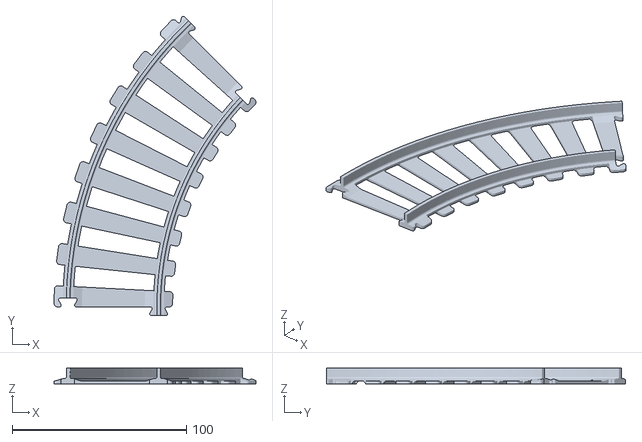
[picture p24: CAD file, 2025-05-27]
CAD&model/rail/R200-45deg (1).stl
115.8 x 171.6 x 9.00

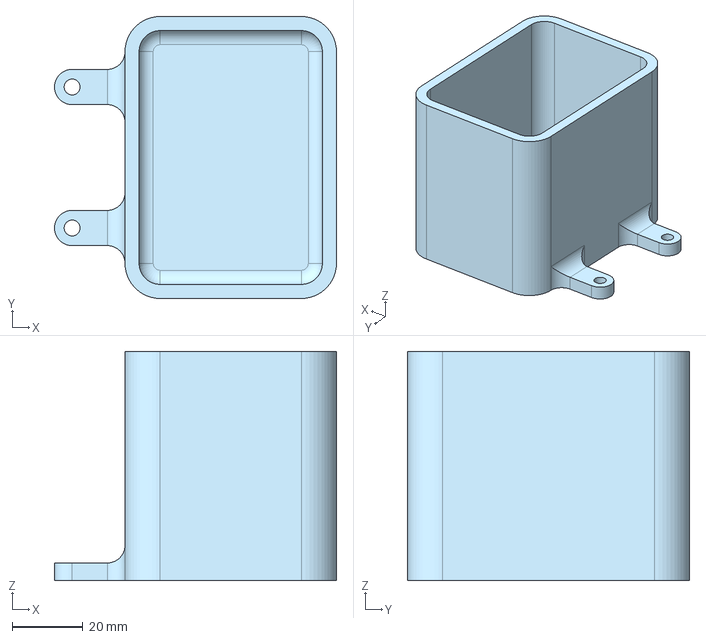
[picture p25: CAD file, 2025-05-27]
CAD&model/water_tank.step
80.0 x 80.0 x 65.0 mm

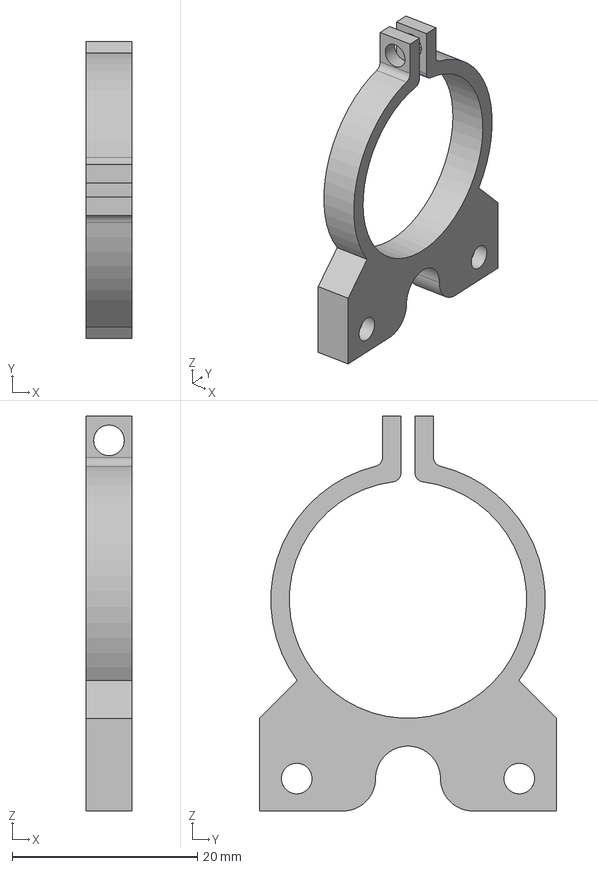
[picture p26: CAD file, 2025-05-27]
CAD&model/water_sensor_holder.step
5.00 x 32.0 x 42.6 mm

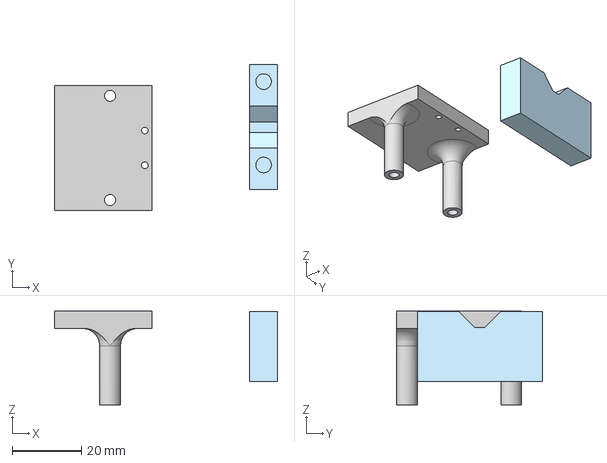
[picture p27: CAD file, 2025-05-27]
CAD&model/magnet_holder&hall_effect_sensor_holder.step
64.2 x 42.0 x 27.0 mm

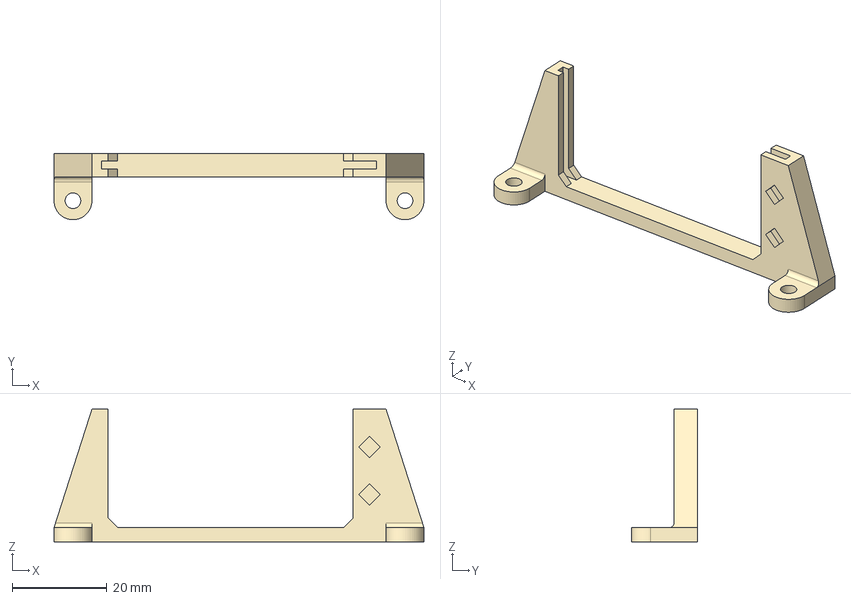
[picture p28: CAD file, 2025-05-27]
CAD&model/curcuit_holder.step
78.0 x 14.0 x 28.0 mm

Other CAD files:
CAD&model/rail/100straight.step
CAD&model/rail/100straight_color_code.step
CAD&model/rail/R200-45deg.step
CAD&model/wheel_set_part.step
CAD&model/Lithium_holder&case.stl
CAD&model/curcuit_holder.stl
CAD&model/lux_sensor_clip_pot.stl
CAD&model/magnet_holder&hall_effect_sensor_holder.stl
CAD&model/motor_drive_holder.step
CAD&model/motor_drive_holder.stl
CAD&model/pot_holder.stl
CAD&model/servo_part_set.stl
CAD&model/station_part.stl
CAD&model/water_sensor_holder.stl
CAD&model/water_tank.stl
CAD&model/watering_part.stl
CAD&model/wheel_set_part.stl

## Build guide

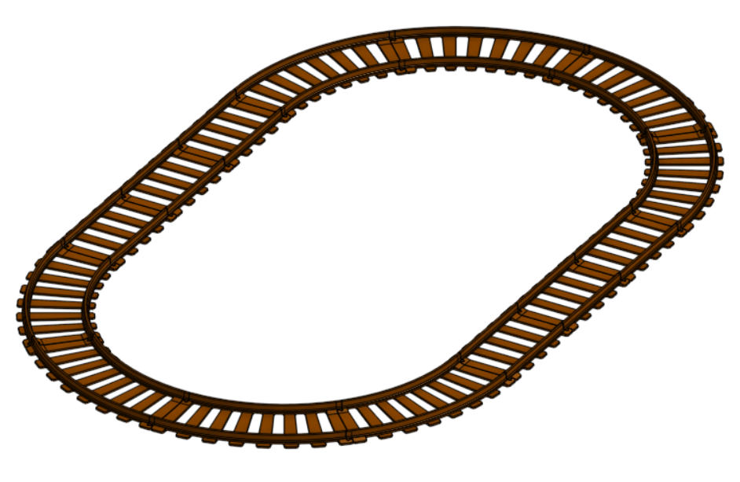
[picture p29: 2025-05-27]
picture/rail-assembly.png
